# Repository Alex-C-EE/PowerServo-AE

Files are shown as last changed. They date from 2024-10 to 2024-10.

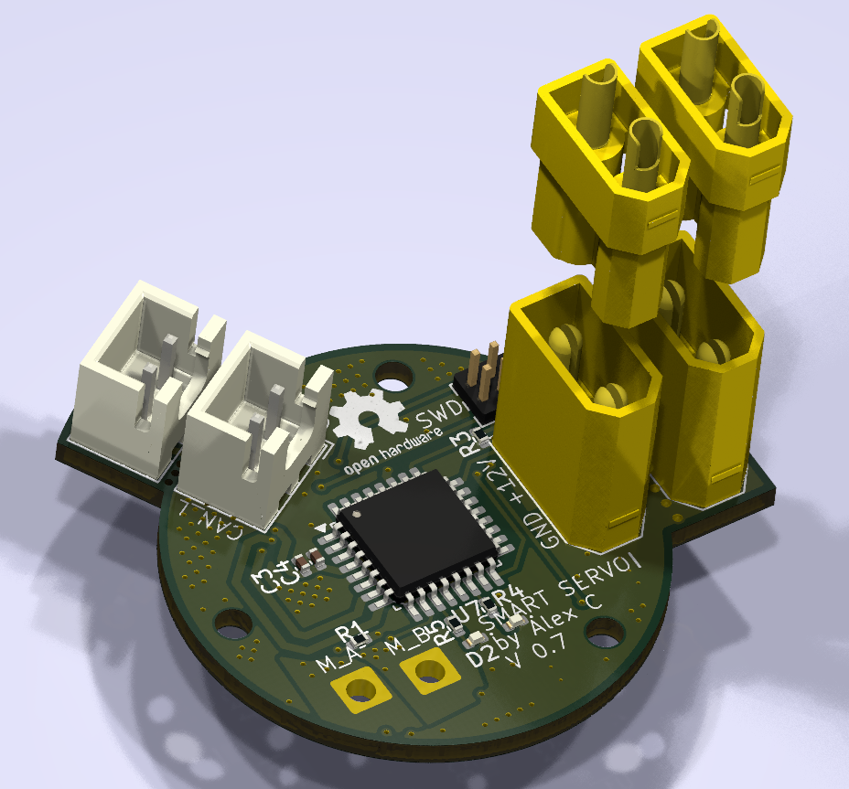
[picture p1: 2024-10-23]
36V 3.6A 30D/CAN-Controlled/Review Request/[22.10.2024]/3D Overview.png

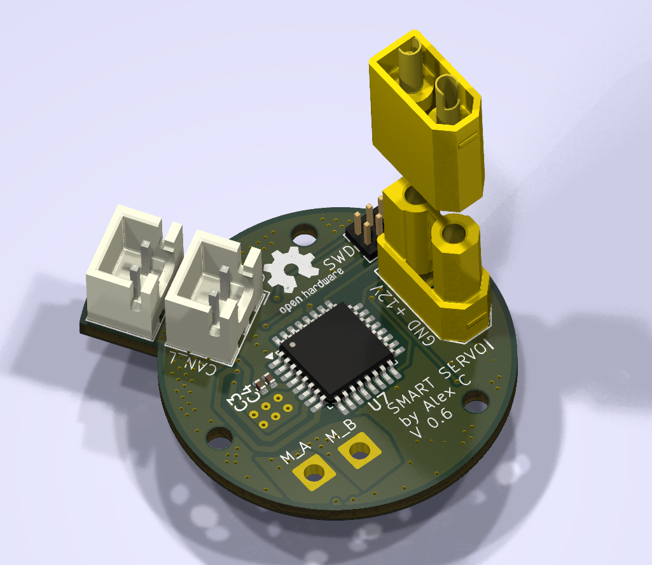
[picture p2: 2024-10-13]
36V 3.6A 30D/CAN-Controlled/Review Request/[13.10.2024] V0.6/3D_Overview.png

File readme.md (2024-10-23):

_This entire project is currently a WIP by a single person, I aim to have a High-Power (12-24V @ 10A) and a Mid Power (6-24V @ 3.6A) version completely done by the end of the year 2024._

_**Really** open to contributors._

**_It would be a REALLY bad idea to try and manufacture anything present here at this time_**

**DCServo AE**

  DCServo AE is an open-source platform designed to effortlessly transform any Brushed DC motor into a continous smart servo with **high precision** and control. Built to provide **high-torque**, **high-RPM**, and accurate positioning through absolute encoding, DCServo AE is a modular solution for hobbyists, roboticists, and makers. 
  The platform allows users to easily drop in a PowerServo AE controller onto a brushed DC motor, turning it into a powerful and precise smart servo, regardless of the motor's size or specifications.

**Project Overview**

  The platform aims to support several variations, including options for high-power, low-power, high(er)-voltage, and low-voltage setups. Each variation is designed to accommodate different performance requirements while maintaining the core features of precise motion control and absolute position feedback. All variations will be based around the **STM32G0** series of microcontrollers due to their **low cost** and **powerful timers and peripherals**. Additionally, all versions will likely use **DRV-series drivers** to ensure robust motor control.

**Core Features**
- Plug and Play: With minimal considerations for design, it is ready to be strapped on the back of any **extended or dual axis/shaft, with magnet** BRUSHED DC Motor and turn it into a Smart Servo Motor.
- Absolute Encoder: PowerServo AE uses magnetic absolute encoders for precise positioning and reliable feedback, eliminating the need for homing or recalibration after power loss.
- Modular Design: Multiple configurations allow for flexibility across a wide range of applications, from lightweight robotics to heavy-duty industrial tasks.
- Open-Source: Both hardware and software are fully open-source, allowing anyone to contribute, modify, and improve the platform.
- Compact Size: The designs are optimized for compactness, with some controllers as small as 12 mm in diameter, making them suitable for space-constrained applications.

**Getting Started**

Clone the Repository:

``git clone https://github.com/Alex-C-EE/DCServo-AE.git``

**Build Your Own:**

- Design files (PCB, schematics) are provided in each version's hardware directory. Design files are in KiCad 8.0 format.
- Code (C, STM32) is provided in each version's software directory.
- GERBERS and BOMs are also provided ready to upload to JLCPCB.

**Documentation**

_WIP, planned control: CAN, UART, PWM_

**Contributing**

We welcome contributions to the PowerServo AE project! Whether you want to improve the hardware, add new features to the firmware, or suggest new variations, feel free to contribute through:

- Issues and Pull Requests on GitHub
- Community discussions in our Discord channel

**License**
- Hardware: Licensed under the CERN Open Hardware License.
- Software: Licensed under the MIT License.

**Join the Community**

_WIP_
Stay updated with the latest developments, tutorials, and community projects:

- Follow on Hackaday.io
- Join the discussion on Discord
- Watch video tutorials and project demos on YouTube

**Similar Projects (and source of inspiration)**

Mechaduino: Similar, but for Steppers specifically
https://hackaday.io/project/11224-mechaduino

MotCTRL: Similar, but for Brushless specifically
https://github.com/osannolik/MotCtrl

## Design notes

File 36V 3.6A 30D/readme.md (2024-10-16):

**TODO:**
- ~~Ensure wider free area around the mounting hole between CAN and XT30~~
- ~~Open Solder Jumper for CAN~~
- ~~Flip XT30 Gender Wise~~
- ~~U2, C7, C8 orientation~~
- ~~Pull Boot0 to ground (10k)~~
- ~~Switch to DRV8251A~~
- ~~Mousebite between data-line~~
  
**REMINDER**
- DO NOT USE FERROMAGNETIC STAND-OFF NEAR A SPINNING MAGNET AND A MAGNETOMETER

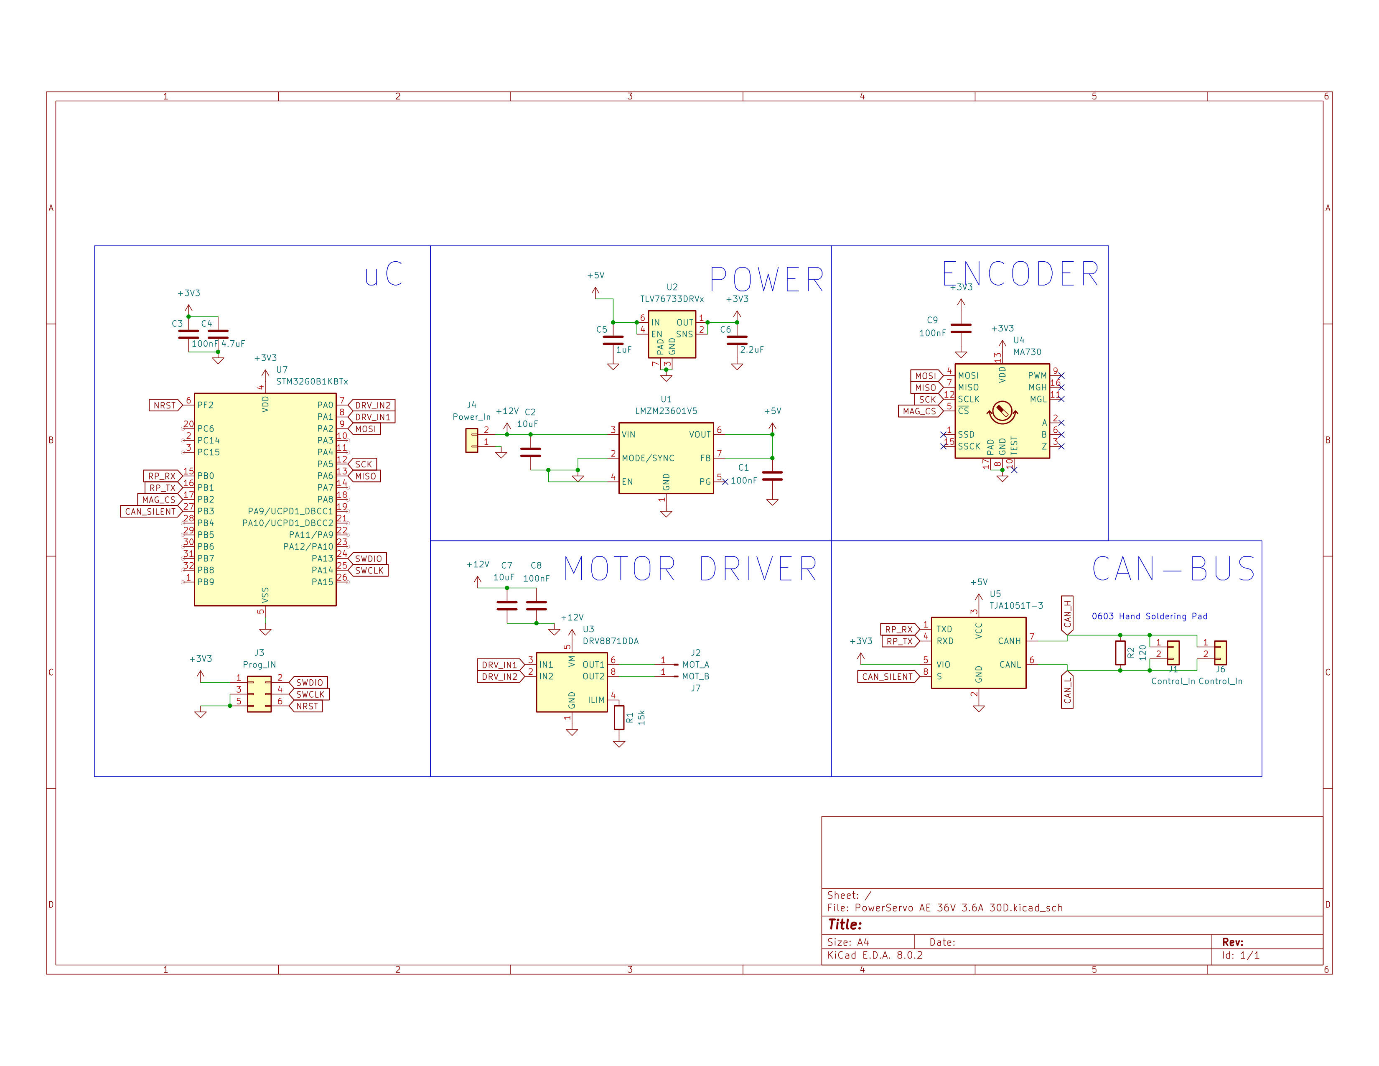
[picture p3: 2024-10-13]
36V 3.6A 30D/CAN-Controlled/Review Request/[13.10.2024] V0.6/Schematic.png

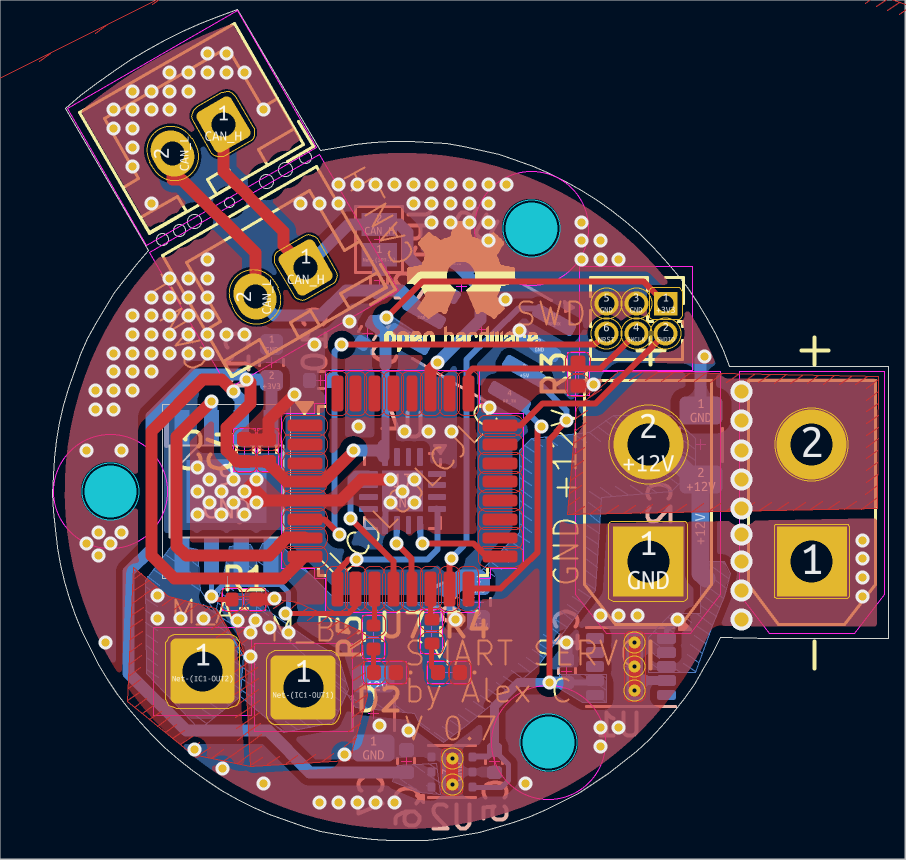
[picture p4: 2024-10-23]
36V 3.6A 30D/CAN-Controlled/Review Request/[22.10.2024]/Front Back.png

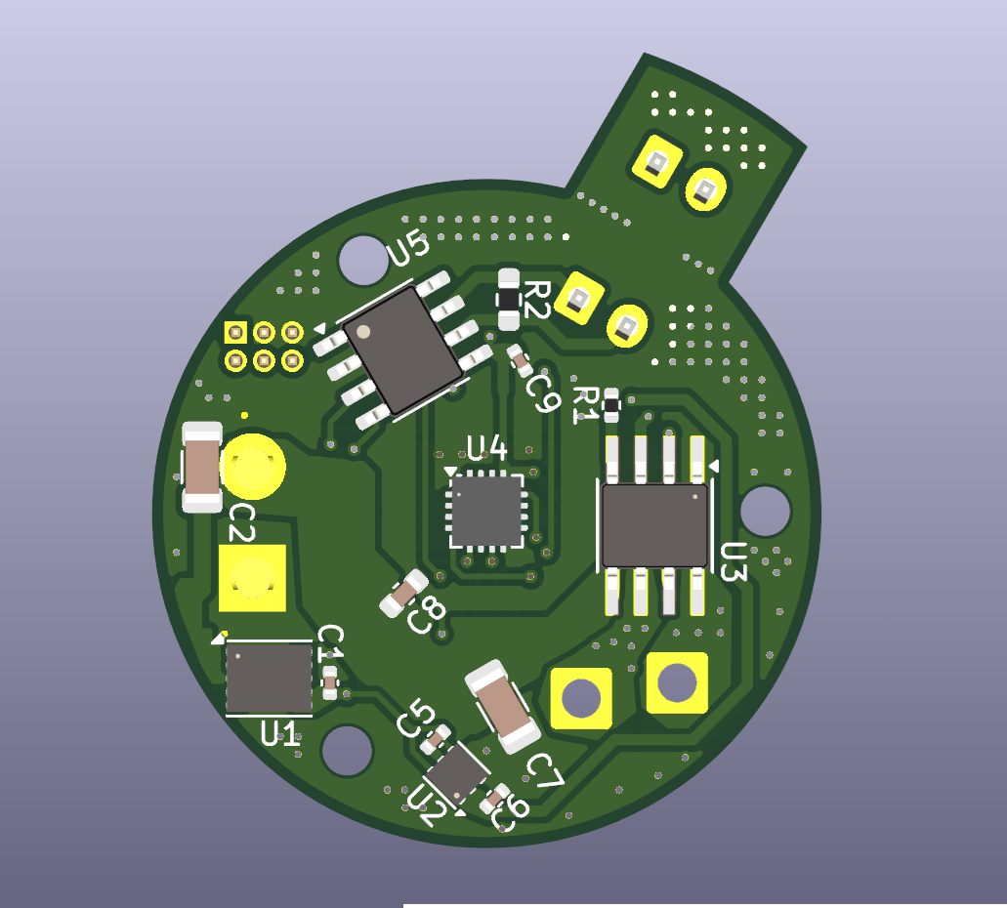
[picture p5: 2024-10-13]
36V 3.6A 30D/CAN-Controlled/Review Request/[13.10.2024] V0.6/3D_Back.png

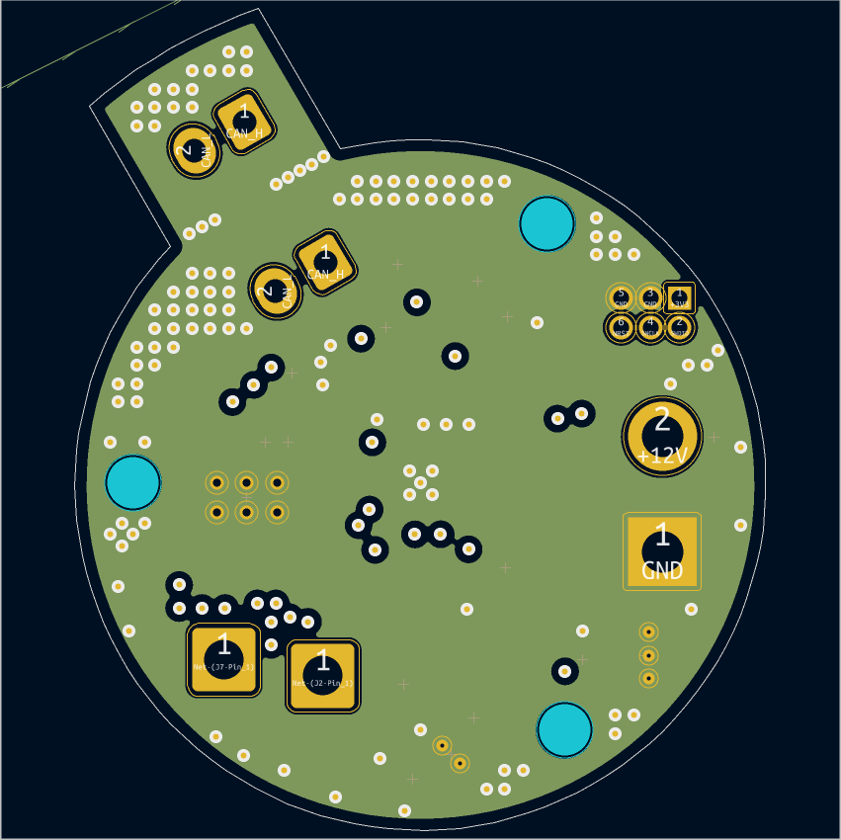
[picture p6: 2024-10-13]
36V 3.6A 30D/CAN-Controlled/Review Request/[13.10.2024] V0.6/IN1+IN2.png

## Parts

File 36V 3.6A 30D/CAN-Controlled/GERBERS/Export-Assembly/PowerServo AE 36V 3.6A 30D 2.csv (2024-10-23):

Comment | Designator | Footprint | LCSC Part Number
100nF | C3,C10,C9,C1 | C_0402_1005Metric
STM32G0B1KBTx | U7 | LQFP-32_7x7mm_P0.8mm
10k | R3 | R_0402_1005Metric
430 | R4,R5 | R_0402_1005Metric
MOT_A | J2 | SolderWire-1sqmm_1x01_D1.4mm_OD2.7mm
4.7uF | C4 | C_0402_1005Metric
15k | R1 | R_0402_1005Metric
Power_In | J5,J4 | AMASS_XT30UPB-M_1x02_P5.0mm_Vertical
Control_In | J6,J1 | JST_XH_B2B-XH-A_1x02_P2.50mm_Vertical
MOT_B | J7 | SolderWire-1sqmm_1x01_D1.4mm_OD2.7mm
LED | D2,D1 | LED_0402_1005Metric
Prog_IN | J3 | PinHeader_2x03_P1.27mm_Vertical
10uF | C7,C2 | C_1206_3216Metric
2.2uF | C6 | C_0402_1005Metric
100nF | C11,C8 | C_0603_1608Metric
TLV76733DRVx | U2 | WSON-6-1EP_2x2mm_P0.65mm_EP1x1.6mm_ThermalVias
DRV8251DDAR | IC1 | SOIC127P600X170-9N
Jumper_2_Open | JP1 | SolderJumper-2_P1.3mm_Open_Pad1.0x1.5mm
TJA1051T-3 | U5 | SOIC-8_3.9x4.9mm_P1.27mm
MA730 | U4 | QFN-16-1EP_3x3mm_P0.5mm_EP1.75x1.75mm
120 | R2 | C_0402_1005Metric
LMZM23601V5 | U1 | Texas_SIL0010A_MicroSiP-10-1EP_3.8x3mm_P0.6mm_EP0.7x2.9mm_ThermalVias
1uF | C5 | C_0402_1005Metric

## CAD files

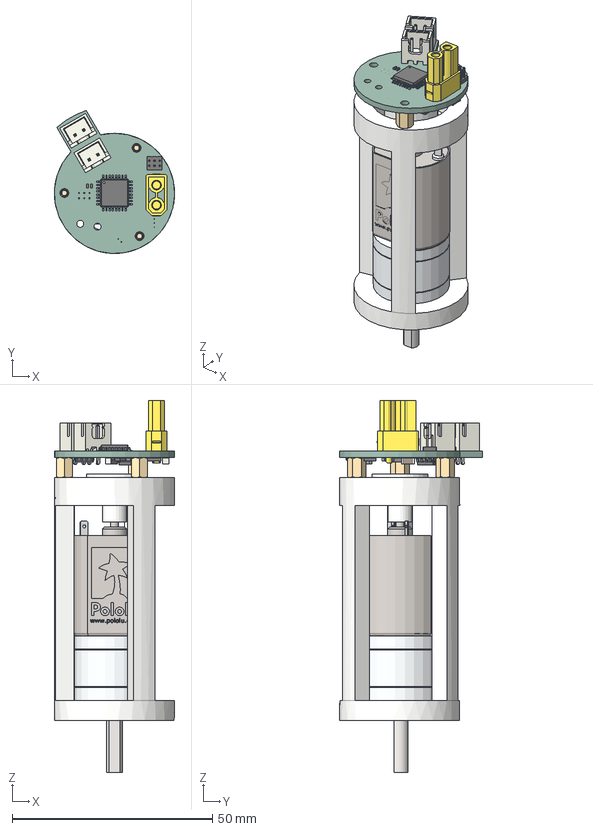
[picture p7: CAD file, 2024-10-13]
36V 3.6A 30D/CAN-Controlled/CAD with Motor/Pololu 20D/Assembly 20D v5.step
30.0 x 35.7 x 92.8 mm
Magnet
C_0402_1005Metric_1 x 6
LQFP_32_7x7mm_P08mm
JST_B2B_XH_A x 2
XT30_Buchse
PinHeader_2x03_P127mm_Vertical
C_1206_3216Metric_1 x 2
Texas_HTSOP_8_1EP_39x49mm_P127mm_EP285x49mm_Mask24x31mm_ThermalVias
WSON_6_1EP_2x2mm_P065mm_EP1x16mm
SOIC_8_39x49mm_P127mm
R_0402_1005Metric_1
C_0603_1608Metric_1
R_0603_1608Metric_1
Texas_SIL0010A_MicroSiP_10_1EP_38x3mm_P06mm_EP07x29mm
PowerServo AE 36V 3.6A 30D_PCB
20d-metal-gearmotor-25-31-with-extended-motor-shaft

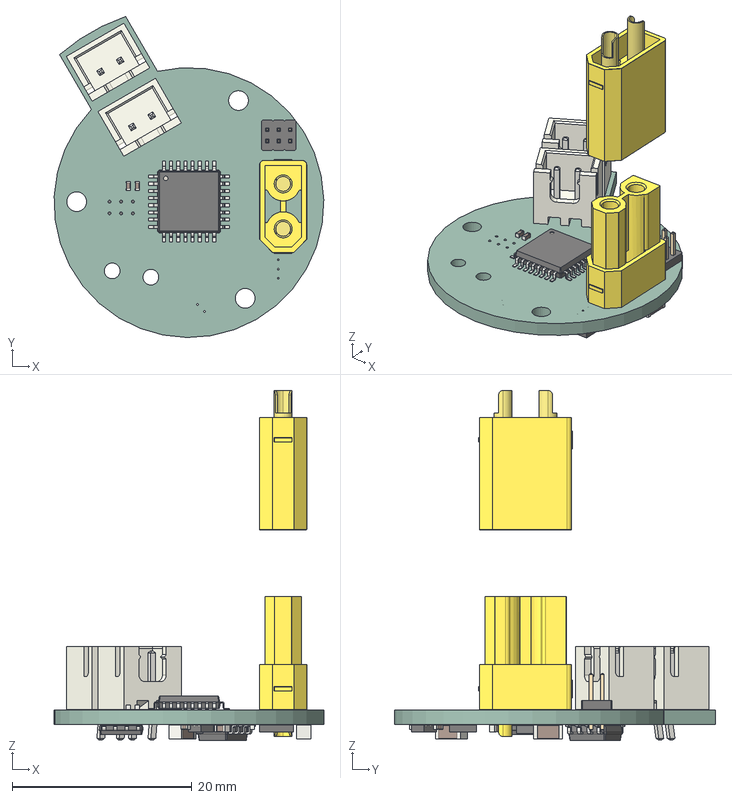
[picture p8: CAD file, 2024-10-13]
36V 3.6A 30D/CAN-Controlled/CAD/PowerServo AE 36V 3.6A 30D CAN - CAD.step
30.0 x 35.7 x 39.0 mm
C_0402_1005Metric x 6
LQFP_32_7x7mm_P08mm
JST_B2B_XH_A x 2
XT30_Stecker
XT30_Buchse
PinHeader_2x03_P127mm_Vertical
C_1206_3216Metric x 2
Texas_HTSOP_8_1EP_39x49mm_P127mm_EP285x49mm_Mask24x31mm_ThermalVias
WSON_6_1EP_2x2mm_P065mm_EP1x16mm
SOIC_8_39x49mm_P127mm
R_0402_1005Metric
C_0603_1608Metric
R_0603_1608Metric
Texas_SIL0010A_MicroSiP_10_1EP_38x3mm_P06mm_EP07x29mm
PowerServo AE 36V 3.6A 30D_PCB

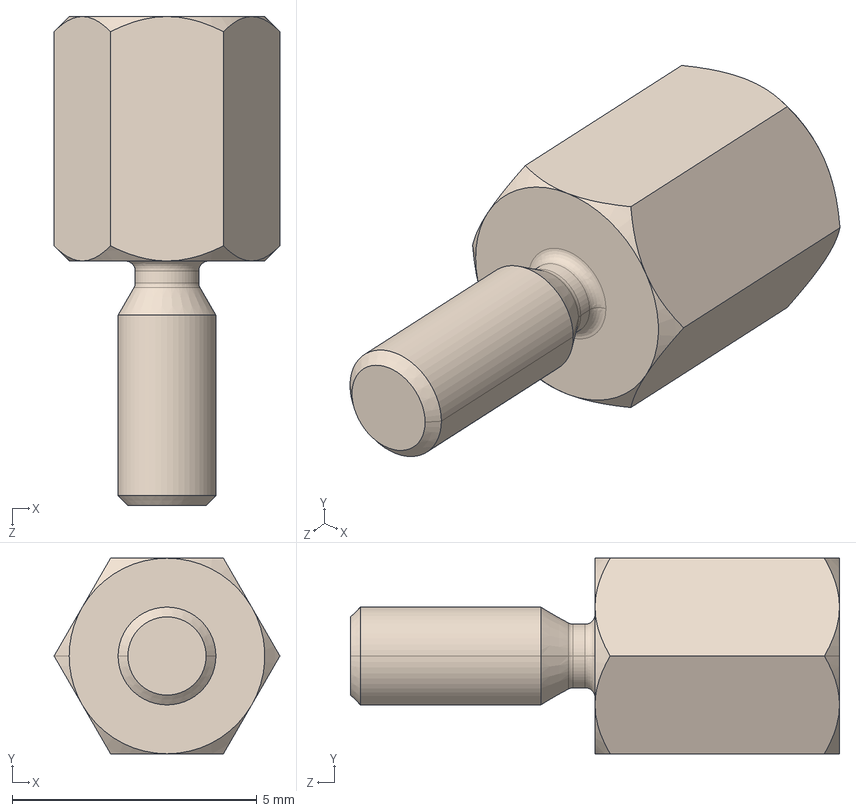
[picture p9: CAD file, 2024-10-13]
General CAD (motors, daughter boards, parametric casings)/Brass Stand-Off M2 x 5mm - 971050244.stp
4.62 x 4.00 x 10.00 mm

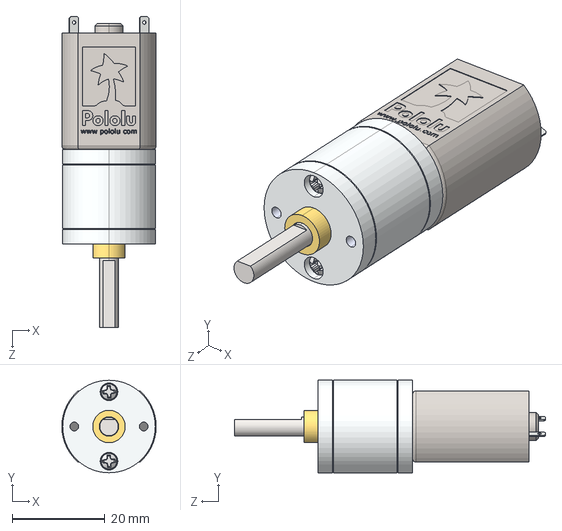
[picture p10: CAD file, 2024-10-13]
General CAD (motors, daughter boards, parametric casings)/Pololu 20D Motors/20d-metal-gearmotor-250-313-391-488.step
20.4 x 20.0 x 67.2 mm

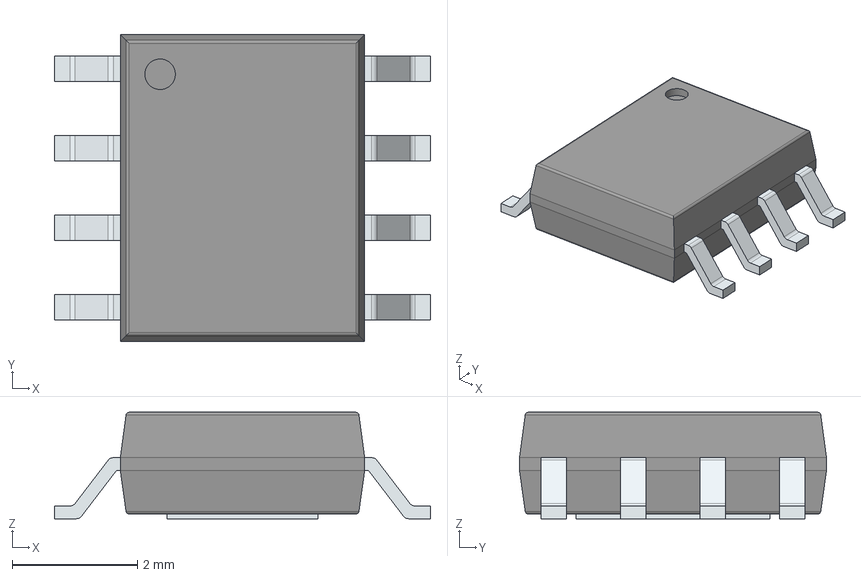
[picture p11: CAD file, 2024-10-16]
General Libraries/DRV8251A/DRV8251DDAR.stp
6.00 x 4.90 x 1.70 mm
PinsArrayLR
ThermalPad

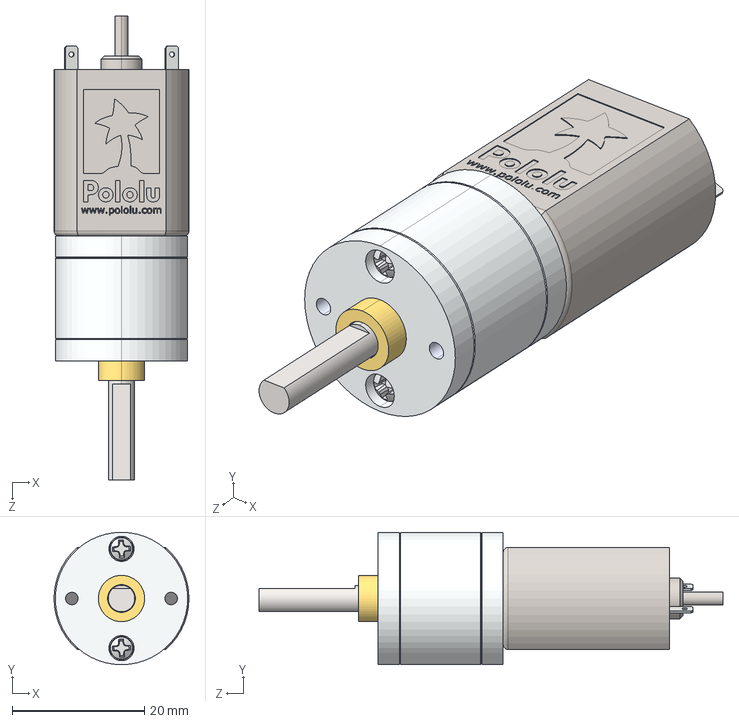
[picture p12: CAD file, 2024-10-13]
General CAD (motors, daughter boards, parametric casings)/Pololu 20D Motors/20d-metal-gearmotor-100-125-156-195-with-extended-motor-shaft.step
20.4 x 20.0 x 70.1 mm

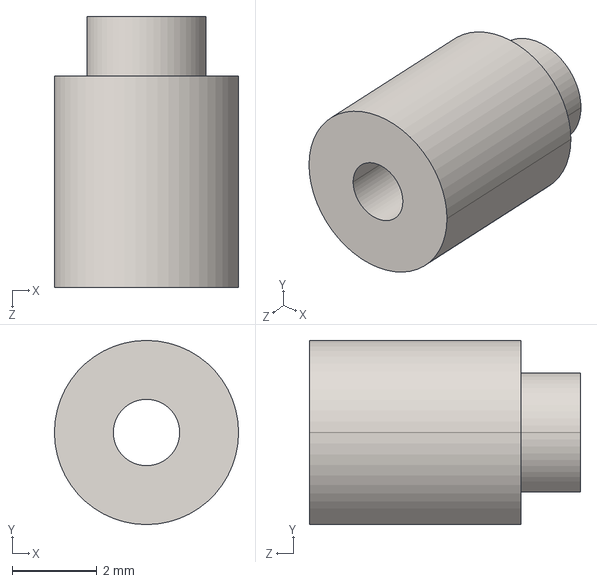
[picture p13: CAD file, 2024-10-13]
General CAD (motors, daughter boards, parametric casings)/Steel Stand-Off M2 x 6.4mm - 9774050243R.stp
4.35 x 4.35 x 6.40 mm

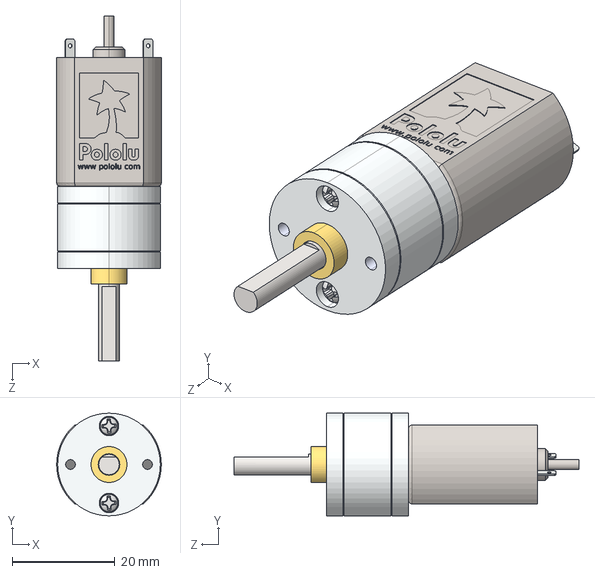
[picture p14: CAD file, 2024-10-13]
General CAD (motors, daughter boards, parametric casings)/Pololu 20D Motors/20d-metal-gearmotor-25-31-with-extended-motor-shaft.step
20.4 x 20.0 x 67.2 mm

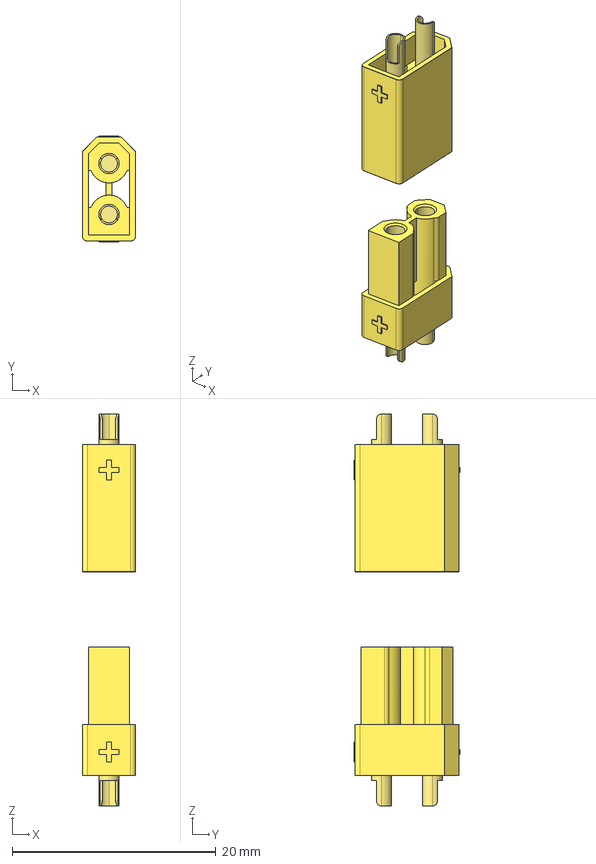
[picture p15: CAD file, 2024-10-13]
General CAD (motors, daughter boards, parametric casings)/XT30.stp
5.25 x 10.4 x 38.5 mm

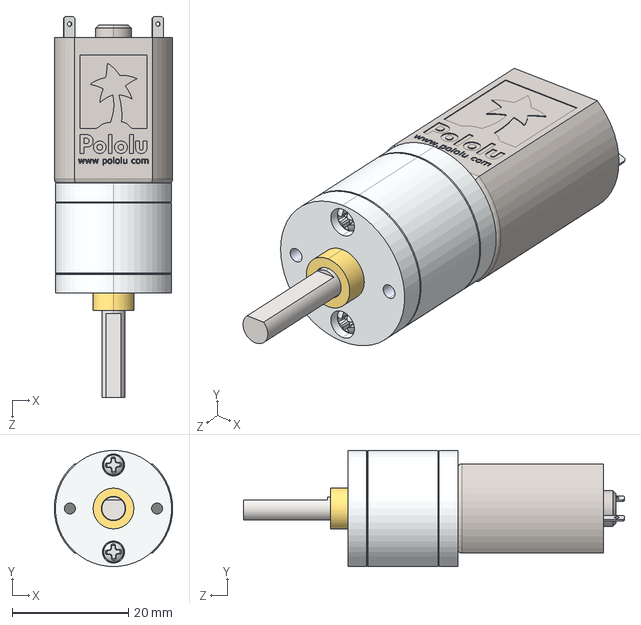
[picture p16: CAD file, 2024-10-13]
General CAD (motors, daughter boards, parametric casings)/Pololu 20D Motors/20d-metal-gearmotor-100-125-156-195.step
20.4 x 20.0 x 65.6 mm

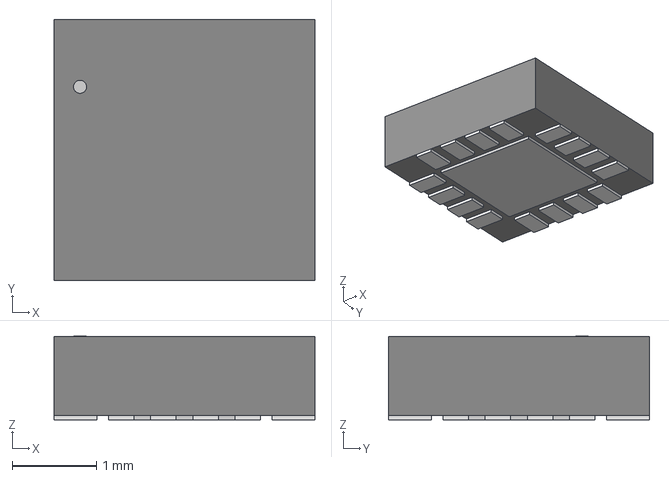
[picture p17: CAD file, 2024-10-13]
General CAD (motors, daughter boards, parametric casings)/QFN-16_MA730_MNP.step
3.10 x 3.10 x 0.993 mm

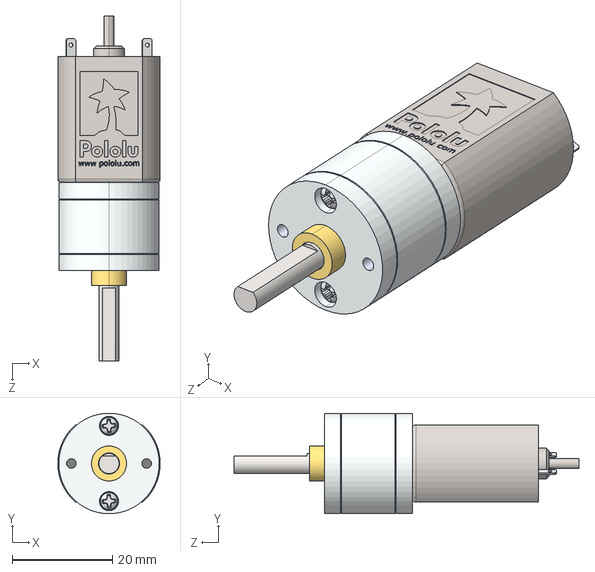
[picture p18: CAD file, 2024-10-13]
General CAD (motors, daughter boards, parametric casings)/Pololu 20D Motors/20d-metal-gearmotor-63-78-with-extended-motor-shaft.step
20.4 x 20.0 x 68.7 mm

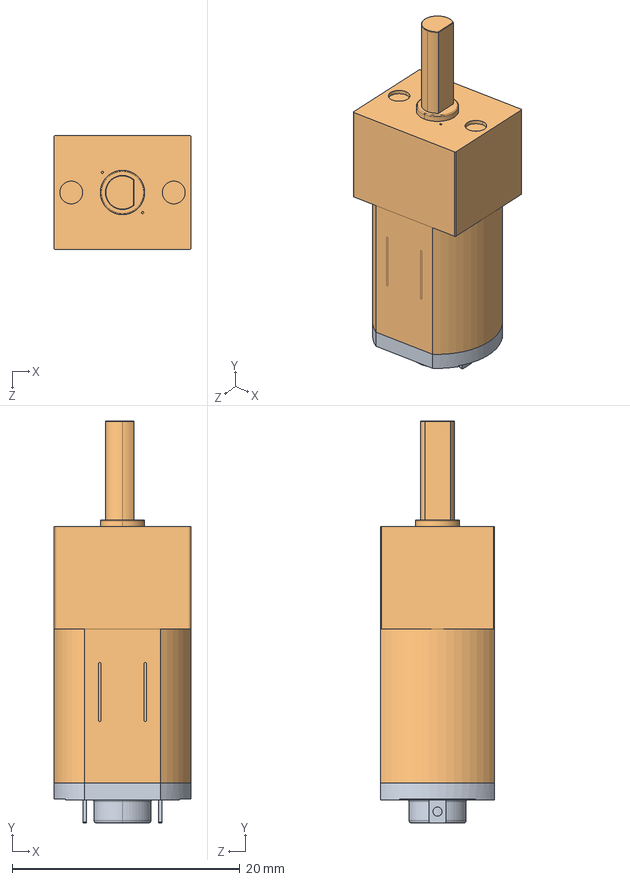
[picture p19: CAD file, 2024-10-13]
General CAD (motors, daughter boards, parametric casings)/Pololu-Micro-Metal-Gearmotor.STEP
12.0 x 35.3 x 10.0 mm

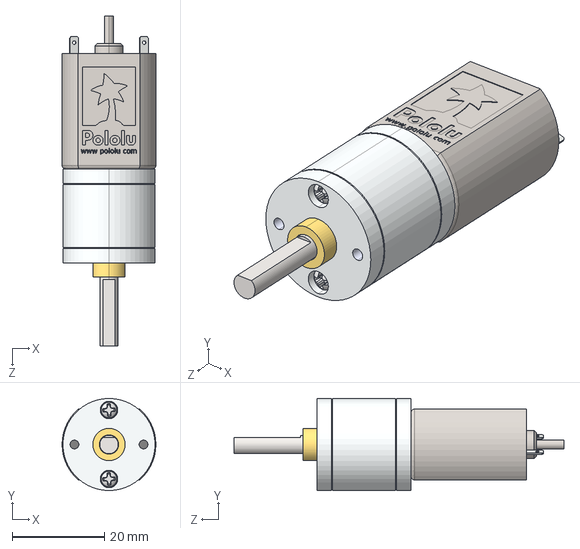
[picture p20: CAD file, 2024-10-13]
General CAD (motors, daughter boards, parametric casings)/Pololu 20D Motors/20d-metal-gearmotor-250-313-391-488-with-extended-motor-shaft.step
20.4 x 20.0 x 71.7 mm

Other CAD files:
General CAD (motors, daughter boards, parametric casings)/Pololu 20D Motors/20d-metal-gearmotor-63-78.step
General CAD (motors, daughter boards, parametric casings)/Pololu 20D Motors/20d-metal-gearmotor-25-31.step

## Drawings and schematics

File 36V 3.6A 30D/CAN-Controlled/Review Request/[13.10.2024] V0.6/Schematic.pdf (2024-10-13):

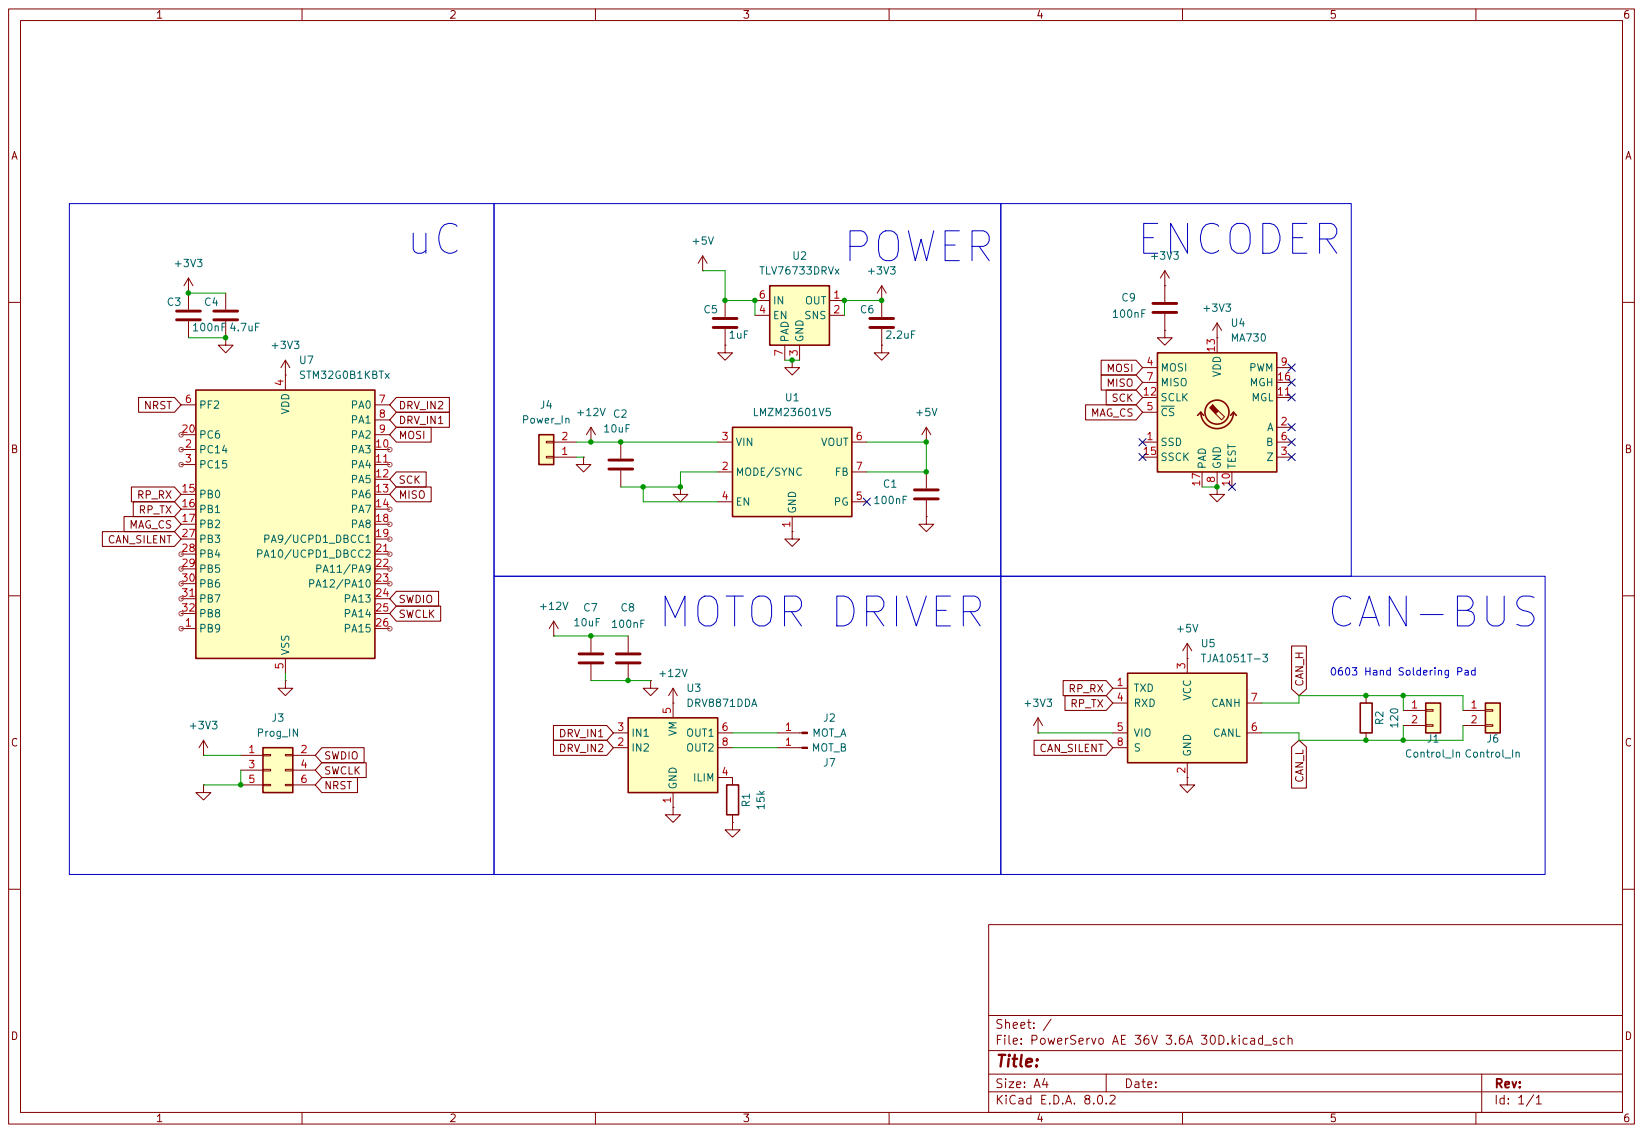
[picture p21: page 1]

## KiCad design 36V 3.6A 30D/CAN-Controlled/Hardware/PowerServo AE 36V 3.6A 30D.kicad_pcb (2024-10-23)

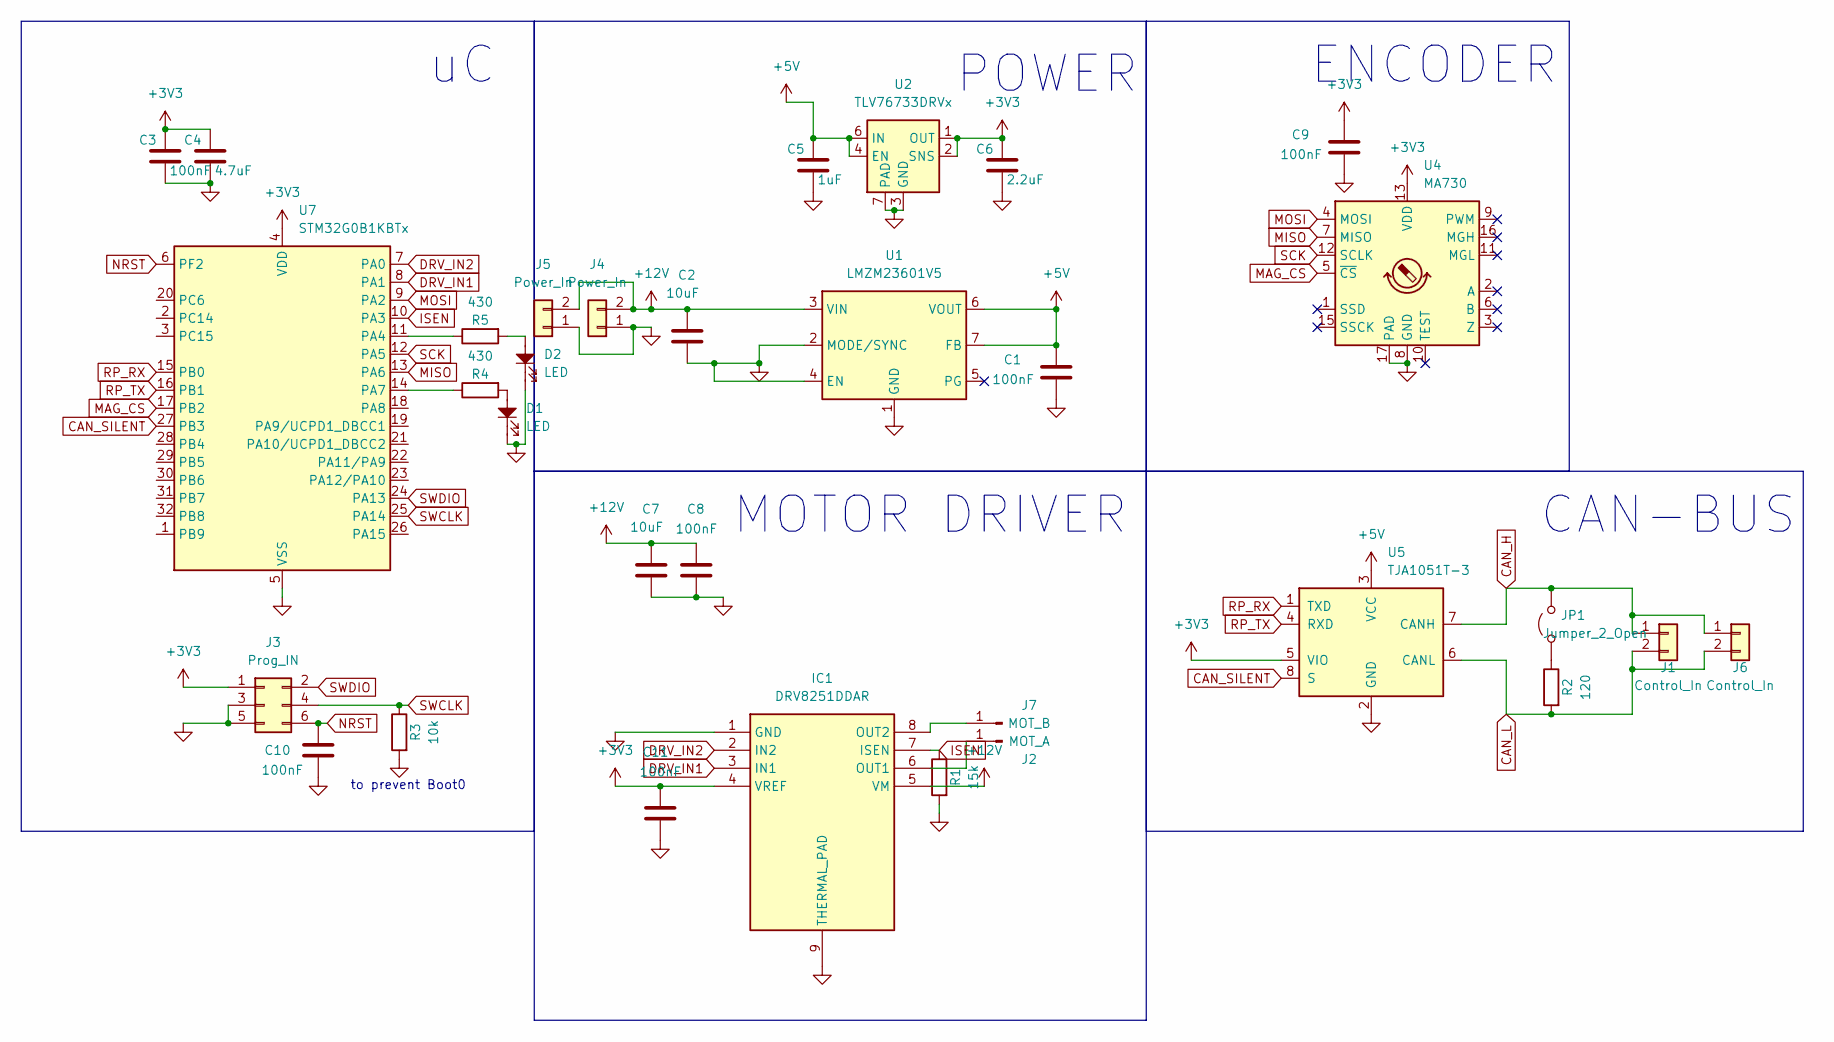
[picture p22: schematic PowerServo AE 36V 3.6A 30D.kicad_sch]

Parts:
C1, C3, C9, C10: 100nF; C_0402_1005Metric
C2, C7: 10uF; C_1206_3216Metric
C4: 4.7uF; C_0402_1005Metric
C5: 1uF; C_0402_1005Metric
C6: 2.2uF; C_0402_1005Metric
C8, C11: 100nF; C_0603_1608Metric
D1, D2: LED; LED_0402_1005Metric
IC1: DRV8251DDAR; SOIC127P600X170-9N; Mouser Part Number 595-DRV8251DDAR
J1, J6: Control_In; JST_XH_B2B-XH-A_1x02_P2.50mm_Vertical
J2: MOT_A; SolderWire-1sqmm_1x01_D1.4mm_OD2.7mm
J3: Prog_IN; PinHeader_2x03_P1.27mm_Vertical
J4, J5: Power_In; AMASS_XT30UPB-M_1x02_P5.0mm_Vertical
J7: MOT_B; SolderWire-1sqmm_1x01_D1.4mm_OD2.7mm
JP1: Jumper_2_Open; SolderJumper-2_P1.3mm_Open_Pad1.0x1.5mm
R1: 15k; R_0402_1005Metric
R2: 120; C_0402_1005Metric
R3: 10k; R_0402_1005Metric
R4, R5: 430; R_0402_1005Metric
U1: LMZM23601V5; Texas_SIL0010A_MicroSiP-10-1EP_3.8x3mm_P0.6mm_EP0.7x2.9mm_T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
U2: TLV76733DRVx; WSON-6-1EP_2x2mm_P0.65mm_EP1x1.6mm_ThermalVias
U4: MA730; QFN-16-1EP_3x3mm_P0.5mm_EP1.75x1.75mm
U5: TJA1051T-3; SOIC-8_3.9x4.9mm_P1.27mm
U7: STM32G0B1KBTx; LQFP-32_7x7mm_P0.8mm

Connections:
+3V3: C3.1, C4.1, C6.1, C9.2, C11.2, IC1.4 (VREF), J3.1, U2.1 (OUT), U2.2 (SNS), U4.13 (VDD), U5.5 (VIO), U7.4 (VDD)
+5V: C1.2, C5.1, U1.6 (VOUT), U1.7 (FB), U2.4 (EN), U2.6 (IN), U5.3 (VCC)
+12V: C2.2, C7.2, C8.2, IC1.5 (VM), J4.2, J5.2, U1.3 (VIN)
CAN_H: J1.1, J6.1, JP1.2 (B), U5.7 (CANH)
CAN_L: J1.2, J6.2, R2.2, U5.6 (CANL)
CAN_SILENT: U5.8 (S), U7.27 (PB3)
DRV_IN1: IC1.3 (IN1), U7.8 (PA1)
DRV_IN2: IC1.2 (IN2), U7.7 (PA0)
GND: C1.1, C2.1, C3.2, C4.2, C5.2, C6.2, C7.1, C8.1, C9.1, C10.1, C11.1, D1.1, D2.1, IC1.1 (GND), IC1.9 (THERMAL_PAD), J3.3, J3.5, J4.1, J5.1, R1.2, R3.2, U1.1 (GND), U1.2 (MODE/SYNC), U1.4 (EN), U1.11 (GND), U2.3 (GND), U2.5 (GND), U2.7 (PAD), U4.8 (GND), U4.17 (PAD), U5.2 (GND), U7.5 (VSS)
ISEN: IC1.7 (ISEN), R1.1, U7.10 (PA3)
MAG_CS: U4.5 (~CS), U7.17 (PB2)
MISO: U4.7 (MISO), U7.13 (PA6)
MOSI: U4.4 (MOSI), U7.9 (PA2)
NRST: C10.2, J3.6, U7.6 (PF2)
unnamed: D1.2, R4.2
unnamed: D2.2, R5.2
unnamed: IC1.6 (OUT1), J2.1
unnamed: IC1.8 (OUT2), J7.1
unnamed: JP1.1 (A), R2.1
unnamed: R5.1, U7.11 (PA4)
unnamed: R4.1, U7.14 (PA7)
RP_RX: U5.1 (TXD), U7.15 (PB0)
RP_TX: U5.4 (RXD), U7.16 (PB1)
SCK: U4.12 (SCLK), U7.12 (PA5)
SWCLK: J3.4, R3.1, U7.25 (PA14)
SWDIO: J3.2, U7.24 (PA13)

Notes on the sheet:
CAN-BUS
to prevent Boot0
POWER
ENCODER
MOTOR DRIVER

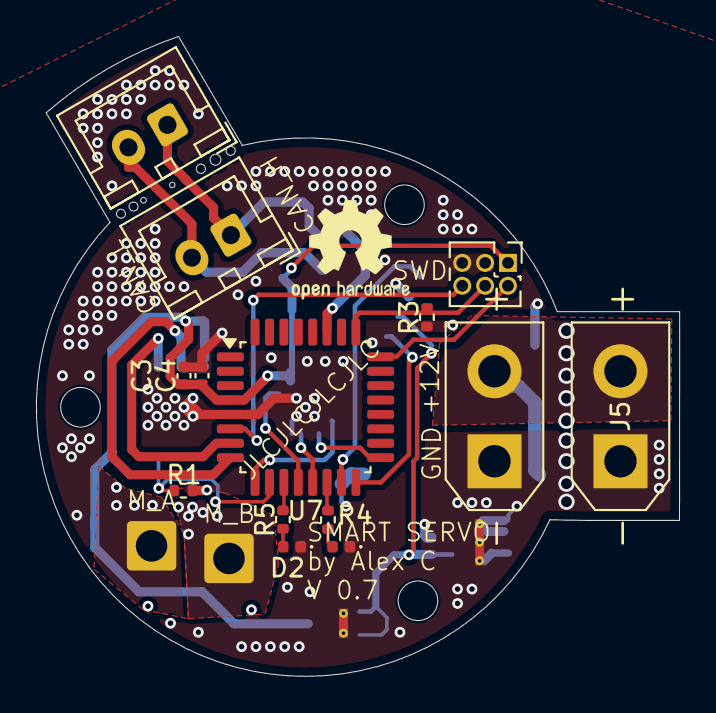
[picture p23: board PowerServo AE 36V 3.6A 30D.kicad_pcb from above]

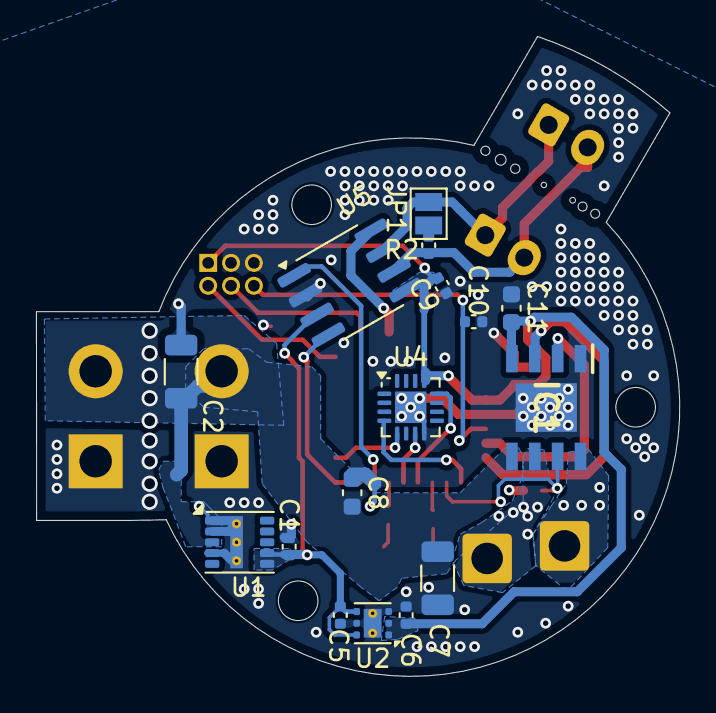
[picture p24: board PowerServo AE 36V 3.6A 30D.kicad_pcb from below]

Board: 4 copper layers, 35.7 x 35.5 mm, 32 parts (16 on the bottom side), 26 nets.

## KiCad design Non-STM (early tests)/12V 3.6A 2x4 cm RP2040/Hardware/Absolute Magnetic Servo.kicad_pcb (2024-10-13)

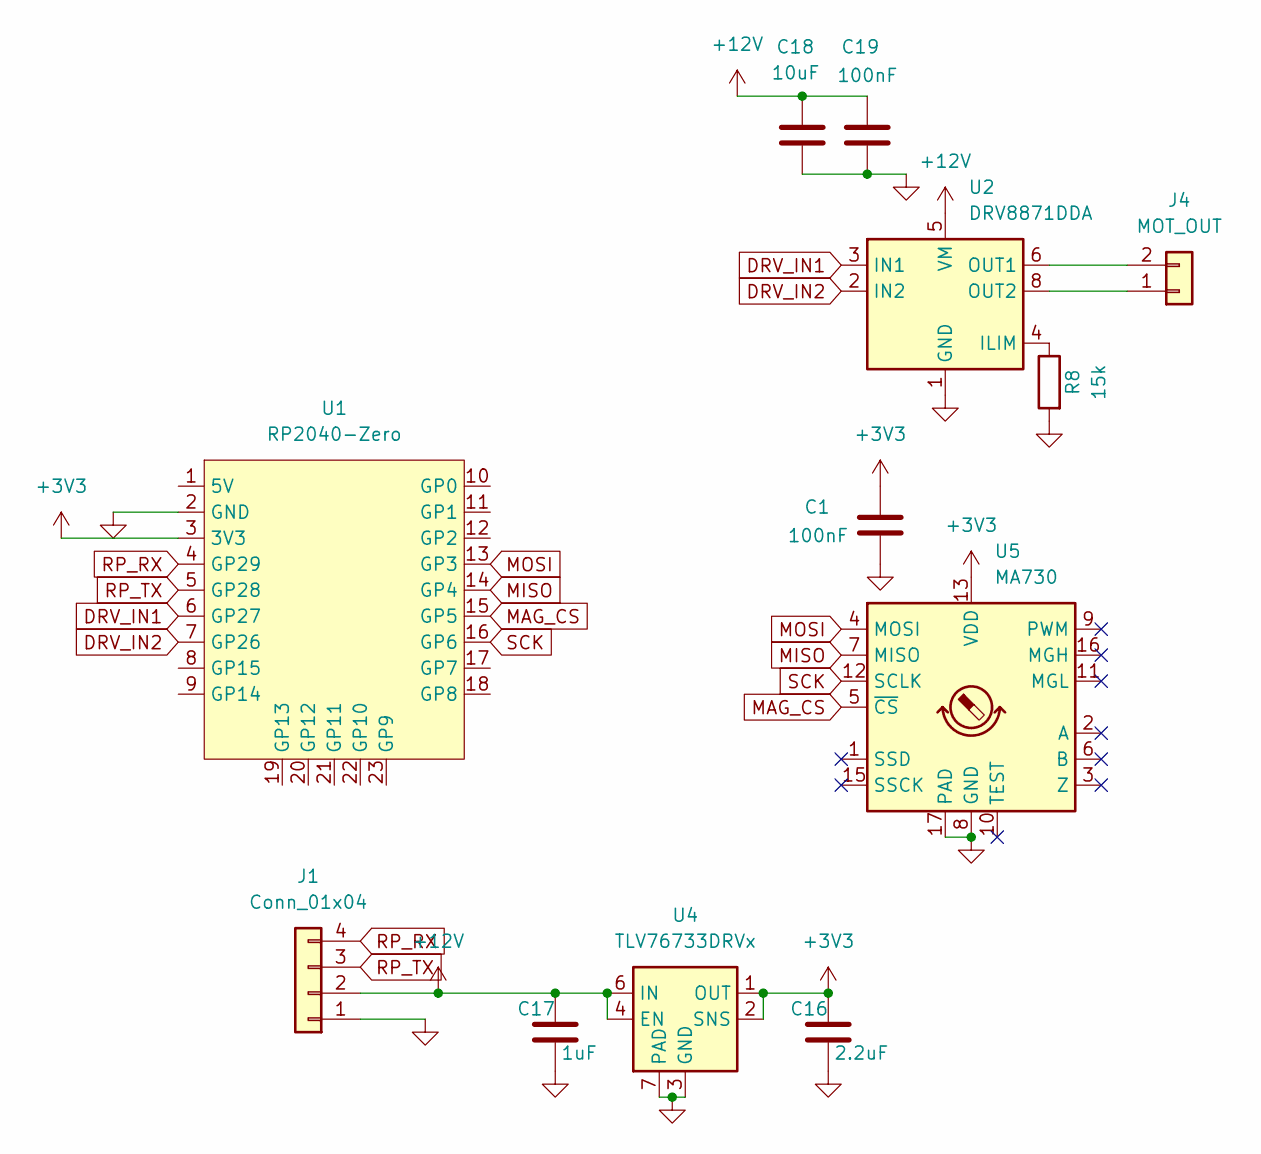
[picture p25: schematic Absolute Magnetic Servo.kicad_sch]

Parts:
C1, C19: 100nF; C_0402_1005Metric
C16: 2.2uF; C_0402_1005Metric
C17: 1uF; C_0402_1005Metric
C18: 10uF; C_0402_1005Metric
J1: Conn_01x04; JST_XH_B4B-XH-AM_1x04_P2.50mm_Vertical
J4: MOT_OUT; PinHeader_1x02_P2.54mm_Vertical
R8: 15k; R_0402_1005Metric
U1: RP2040-Zero; RP2040 Zero
U2: DRV8871DDA; Texas_HTSOP-8-1EP_3.9x4.9mm_P1.27mm_EP2.95x4.9mm_Mask2.4x3.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
U4: TLV76733DRVx; WSON-6-1EP_2x2mm_P0.65mm_EP1x1.6mm_ThermalVias
U5: MA730; QFN-16-1EP_3x3mm_P0.5mm_EP1.75x1.75mm

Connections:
+3V3: C1.2, C16.1, U1.3 (3V3), U4.1 (OUT), U4.2 (SNS), U5.13 (VDD)
+12V: C17.1, C18.2, C19.2, J1.2, U2.5 (VM), U4.4 (EN), U4.6 (IN)
DRV_IN1: U1.6 (GP27), U2.3 (IN1)
DRV_IN2: U1.7 (GP26), U2.2 (IN2)
GND: C1.1, C16.2, C17.2, C18.1, C19.1, J1.1, R8.2, U1.2 (GND), U2.1 (GND), U2.7 (GND), U2.9 (GND), U4.3 (GND), U4.5 (GND), U4.7 (PAD), U5.8 (GND), U5.17 (PAD)
MAG_CS: U1.15 (GP5), U5.5 (~CS)
MISO: U1.14 (GP4), U5.7 (MISO)
MOSI: U1.13 (GP3), U5.4 (MOSI)
unnamed: J4.1, U2.8 (OUT2)
unnamed: J4.2, U2.6 (OUT1)
unnamed: R8.1, U2.4 (ILIM)
RP_RX: J1.4, U1.4 (GP29)
RP_TX: J1.3, U1.5 (GP28)
SCK: U1.16 (GP6), U5.12 (SCLK)

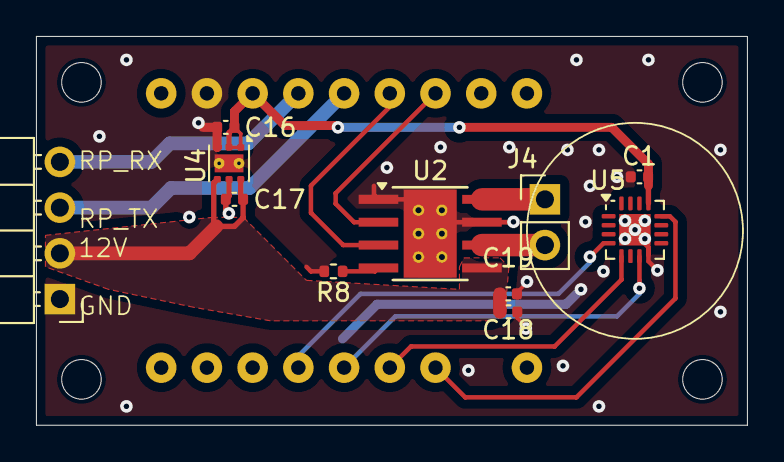
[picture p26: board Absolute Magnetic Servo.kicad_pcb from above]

Board: 4 copper layers, 39.5 x 21.6 mm, 12 parts (1 on the bottom side), 14 nets.

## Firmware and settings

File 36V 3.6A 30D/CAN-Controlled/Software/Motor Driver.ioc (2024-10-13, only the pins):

Mcu.UserName=STM32G0B1KBTx
PA0.Signal=S_TIM2_CH1_ETR
PA1.Signal=S_TIM2_CH2
PA13.Signal=SYS_SWDIO
PA14-BOOT0.Signal=SYS_SWCLK
PA2.Signal=SPI1_MOSI
PA5.Signal=SPI1_SCK
PA6.Signal=SPI1_MISO
PA7.Signal=GPIO_Output
PB0.Signal=FDCAN2_RX
PB1.Signal=FDCAN2_TX
PB2.Signal=GPIO_Output

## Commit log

2024-10-13 Initial Commit Basically
    [Absolute Magnetic Servo Modular STM32.kicad_pcb, Absolute Magnetic Servo Modular STM32.kicad_sch, Absolute Magnetic Servo.kicad_pcb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]
2024-10-13 Added STM32CubeIDE Project
2024-10-13 Review Request Files and Preparations
    [PowerServo AE 36V 3.6A 30D.kicad_pcb, PowerServo AE 36V 3.6A 30D.kicad_sch]
2024-10-13 CAD Stuff
    [20d-metal-gearmotor-100-125-156-195-with-extended-motor-shaft.step, 20d-metal-gearmotor-100-125-156-195.step, 20d-metal-gearmotor-25-31-with-extended-motor-sha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]
2024-10-13 Fixed U2 / C7 Orientation
    [PowerServo AE 36V 3.6A 30D.kicad_pcb]
2024-10-13 Bumped to V0.7
    Following Reddit Review:
    - Added C10 as NRST Cap
    - Added R3 as Boot0/SWCLK Pull-Down
    - Added Solder Jumper for CAN Termination
    -- Downscaled R2
    - Fixed some of the odd orientations of components
    [PowerServo AE 36V 3.6A 30D.kicad_pcb, PowerServo AE 36V 3.6A 30D.kicad_sch]
2024-10-14 I forgor
    [PowerServo AE 36V 3.6A 30D.kicad_pcb]
2024-10-16 STM32 Code Update
    Motor_Control Module kinda done -> TODO: ADC read via DMA
2024-10-16 Finalized Reddit TODO
    [DRV8251DDAR.stp, PowerServo AE 36V 3.6A 30D.kicad_sch]
2024-10-17 Dev Version for Tests
    [PowerServo AE 36V 3.6A 30D - DEV.kicad_pcb, PowerServo AE 36V 3.6A 30D - DEV.kicad_sch, PowerServo AE 36V 3.6A 30D.kicad_pcb]
2024-10-21 Flowchart update. PCB Update to include 2nd XT30
    [PowerServo AE 36V 3.6A 30D.kicad_pcb, PowerServo AE 36V 3.6A 30D.kicad_sch]
2024-10-23 Starting High Power Hardware while I wait for PCBs to arrive
    [36V 10A.kicad_pcb, 36V 10A.kicad_sch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]
2024-10-23 Solved DRC
    [PowerServo AE 36V 3.6A 30D.kicad_pcb]
